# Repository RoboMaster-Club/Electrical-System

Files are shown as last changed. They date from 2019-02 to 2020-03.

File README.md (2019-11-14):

# Robomaster Electrical System Repo
Welcome to Purdue Robomaster Club's Electrical System Repository Created by Chengming Zhang. This repository contain everything from PCB design, Design Notebook (In sub-folder's ReadMe.md), and softwares. 

If you are not familier with Robomaster, or Purdue's Robomaster Team, please refer to [Our Website](https://www.PurdueRM.com "Purdue Robomaster") or check out this video covered by **The Verge**.

<br><br>

<iframe width="560" height="315" src="https://www.youtube.com/embed/ECr4zgK6cPA" frameborder="0" allow="accelerometer; autoplay; encrypted-media; gyroscope; picture-in-picture" allowfullscreen></iframe>

## Team Structure

**Electrical Team Lead**: Chengming Zhang ` @cmz97` 

**Active Member:**

Henry Silva ` @Lazloian` 

Dansen Wang ` @cmz97` 

MingCheng Li ` @blaticslm` 

Ben Mirvish ` @bmivish` 

## Project Structure

📣**For detail design notebook, pls visit the coresponding directory**📣

▶️ Work in-Progress

🔜 Future Project

🉑 Completed Project

🔂 New Iteration

‼️ Need Documentation

⚠️ Ship Blocker

🚮 Abanded Project

<br><br>

The image bellow is our latest **Electrical System Diagram** which lays out all the connection between our subsystems.

 

## Power Electronics

### Super Capacitor Bank ‼️ ▶️ ⚠️

 `Made by @bmirvish @blaticslm`

Due to the competition rule, the robot chassis, which consists of four DJI 3508 geared brushless motor, can not draw more than 240W of power at any given time. To overcome this limitation, we designed our custom made supercapacitor bank as a buffer that provides instantaneous power to our robot on demand. **This Capacitor Bank only consist of voltage banlancing circuit, ADC, and the Super Capacitor Unit.** Since this is a passive electrical unit, there is no firmware.

> Plan for your PCB, Electrical Parameter and Mechinical Parameters like dimentions in your own folder‼️

> * PCB Design  @#todo‼️
> * CAD Design Enclosure @#google drive link‼️

<br>

### Super Capacitor Charger (STM32) ‼️ 🔜 ⚠️ 🔂

`Made by @cmz97`

Since Capacitor is a short circuit when not charged, we need to design a consitance current charger to avoid damage of the battery and capacitor. Chengming Selected to use a H bridge Configuration to create a custon buck convertor using STM32F334. Currently, the Super Capacitor Charger can takes any voltage between 5v - 50v and convert it to 1v - 40v. The maxium output current is 10A. The PCB has a dimension of 2.599 in x 2.487 in and four layer. 

<br>

PCB Design @[SuperCapacitor-v2.0](https://github.com/RoboMaster-Club/Electrical-System/tree/master/SuperCapacitor-v2.0)

Firmware @[SuperCapacitor-v2.0](https://github.com/RoboMaster-Club/Electrical-System/tree/master/SuperCapacitor-v2.0)

<br>

### Power Distribution Boards 🉑

Power Distribution Board is used to distribute electrical current in different voltage across the robot. Currently the Robot takes the following voltage level. 

> **24 Volt** for Robot controller, Any motor

> **12 Volt** for Jetson TX 2, Transparent OLED

> **5 Volt** for Gimbal Electrical Controller Board (ATMEGA), Electrical System Controller(ESP32)

> **3.3 Volt** for all the embedded chip, STM32F4, ESP32, ATMEGA

> **1.5 Volt** for Ammo remaining detection circuit

For a more accurate and compelete report on voltage and current usage of our robot, pls refer to [Power Distribution Board Design Log](https://github.com/RoboMaster-Club/Electrical-System/blob/master/Power-Distribution-Board-V3.0/README.md)

The newst power distribution board is divided into three seperated board:

<br>

### Chassis Power Distribution Board

`Made by @cmz97`

This board provides all the power delivery on the robot chassis, which consist of four DJI M3508 Motor. It also has a 3.3v relay on board that selection output from either the super capacitor bank or the battery directorly. This switching action can be controlled by software via a logic high, which is passed through a opto-isolator  for signal isolation. In case of emergency, such as super capacitor failure, one can flip a by-pass switch that disable all software input, and force the circuit to take battery input only. 

<br><br>

The software switch is controlled by the Electrical System Controller (STM32/ESP32) that switch the output dynamically according to the current power usage. In seniorio such as low votage on super capacitor, Electrical System Controller can select battery input to avoid damage to the supercapacitor, and left it for charging. 

[Chassis Power Distribution Board  Repository for Detail Info](https://github.com/RoboMaster-Club/Electrical-System/tree/master/Power-Distribution-Board-V3.0/Chassis%20Power%20Distribution%20Board)‼️

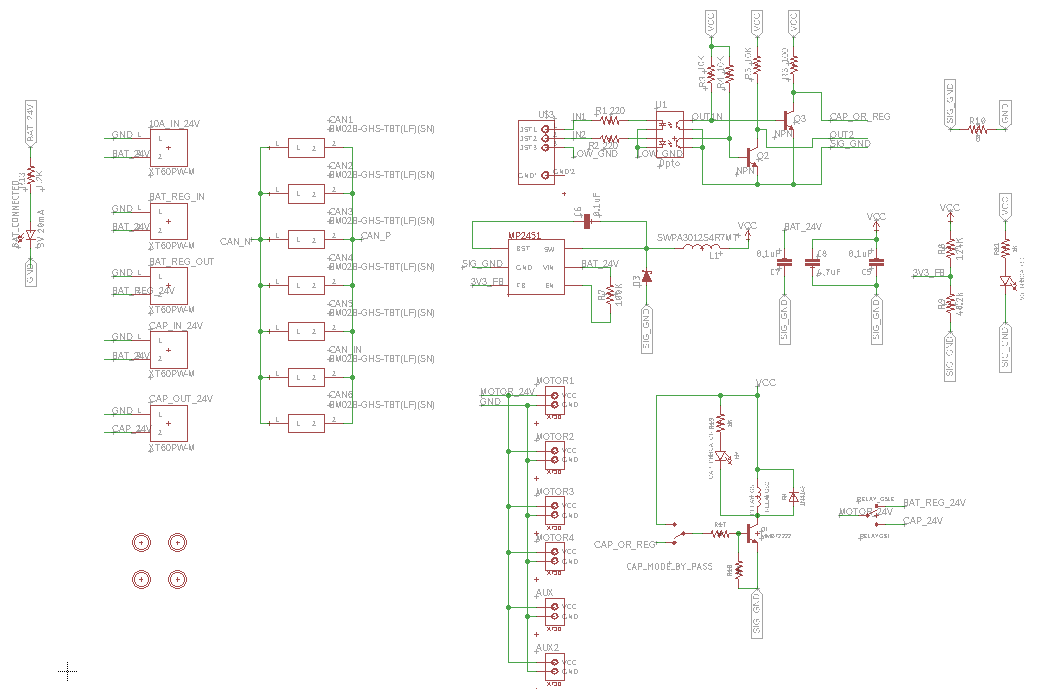
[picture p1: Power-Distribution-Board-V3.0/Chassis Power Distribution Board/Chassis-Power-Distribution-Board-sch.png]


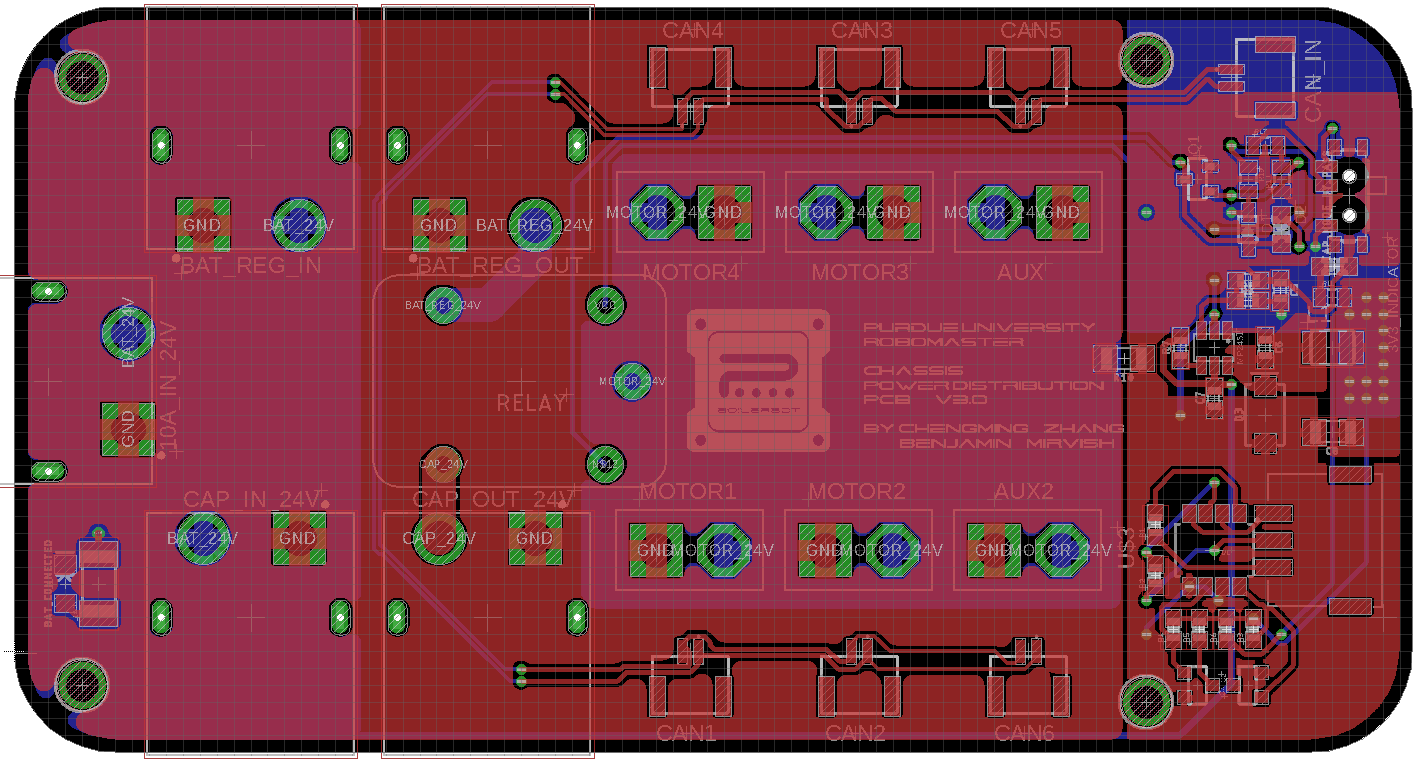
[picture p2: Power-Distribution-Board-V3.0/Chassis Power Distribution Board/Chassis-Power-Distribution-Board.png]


<br>

### Slip-Ring Power Distribution Board

`Made by @cmz97`

This board provides power to the Pitch Motor for the gimbal system, as well as power for Electrical System Controller. The board also provides pre-organization of the wires that go up through the slip-ring. Slipring is used in the robot due to mechanical constraints, where the robot's gimbal needs to rotate continuously. Since there are only 24 wires passess through the slipring used in our standard robot, with each of the wire capable of carring 2A of maxium continouse current, proper signal allocation need to be conducted. <br><br>

We concluded the following wiring asssignment:

| Signal Name | 8A Power | 8A GND | 4A Power | 4A GND | Motor CAN H | Motor CAN L | REF_TX | REF_RX | GPIO | ESP32_TX | Referee System | Ammo Boost |
| --- | --- | --- | --- | --- | --- | --- | --- | --- | ---- | --- | --- | --- |
| # of Wire | 4 | 4 | 2 | 2 | 1 | 1 | 1 | 1 | 1 | 1 | 4 | 2 |
| Max Current (A) | 8 | 8 | 4 | 4 | 2 | 2 | 2 | 2 | 2 | 2 | 2 | 2 |

<br><br>

[SlipRing Distribution Board Repository for Detail Info](https://github.com/RoboMaster-Club/Electrical-System/tree/master/Power-Distribution-Board-V3.0/SlipRing%20Distribution%20Board)

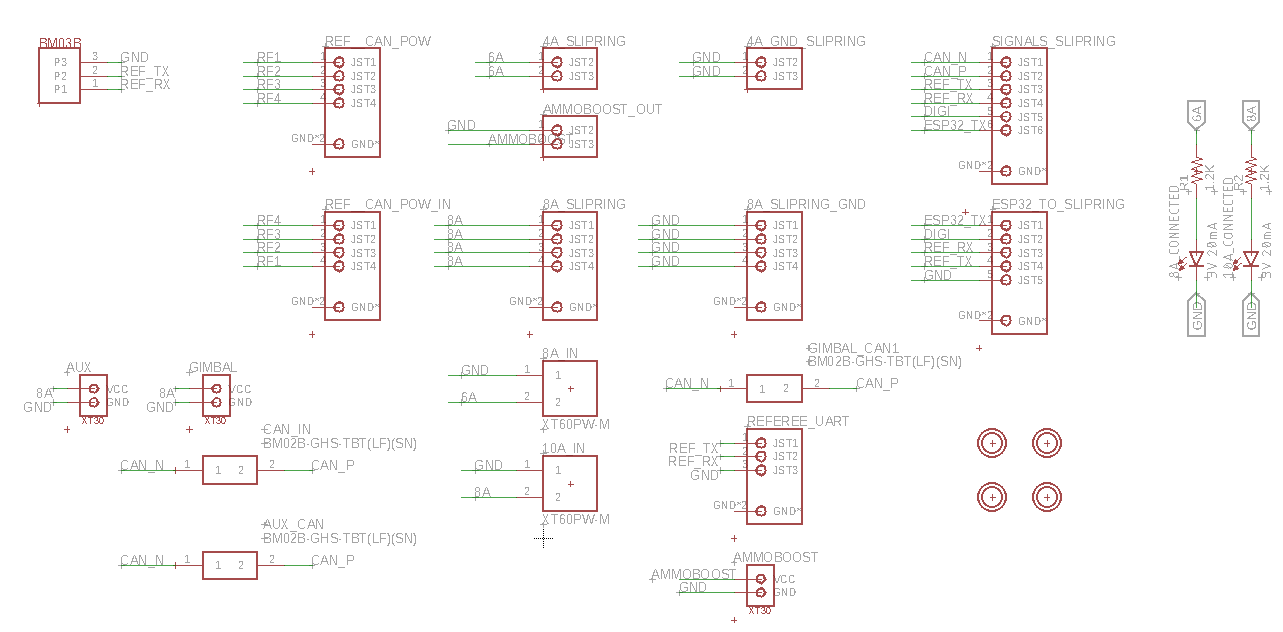
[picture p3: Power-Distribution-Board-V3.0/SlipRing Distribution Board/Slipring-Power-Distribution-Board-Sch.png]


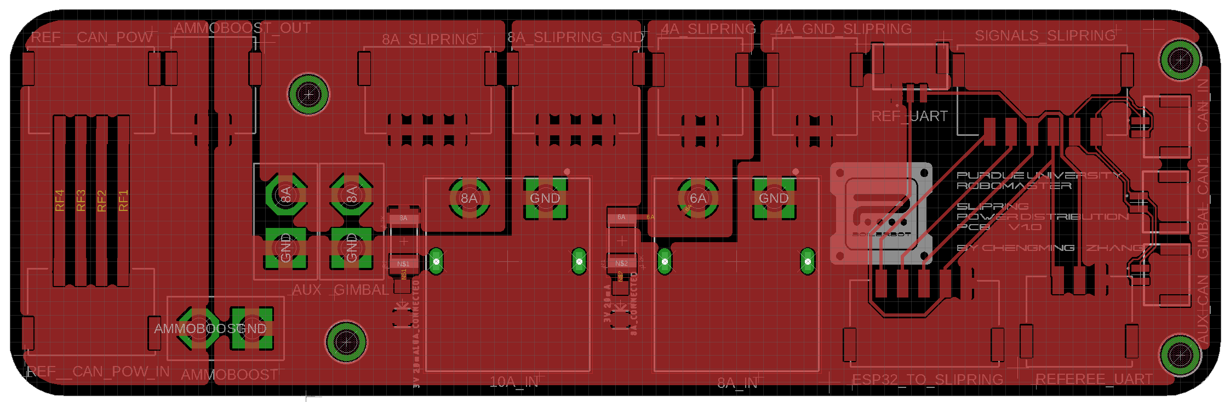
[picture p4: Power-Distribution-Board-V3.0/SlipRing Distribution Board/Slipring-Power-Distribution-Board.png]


<br>

### Gimbal Power Distribution Board

`Made by @cmz97`

This board provides power to the STM32 Robot controller, JetsonTX2, Yall Motor, Flywheel, ammo motor, as well as the Gimbal Electrical System Controller. On board this board, there are two MP1584EN buck convertor that converts 24v from the battery to 12v for Tx2 and 5v for the Gimbal Electrical System Controller.

[Robomater Gimbal Power Distribution Board Repository for Detail Info](https://github.com/RoboMaster-Club/Electrical-System/tree/master/Power-Distribution-Board-V3.0/Robomater%20Gimbal%20Power%20Distribution%20Board)

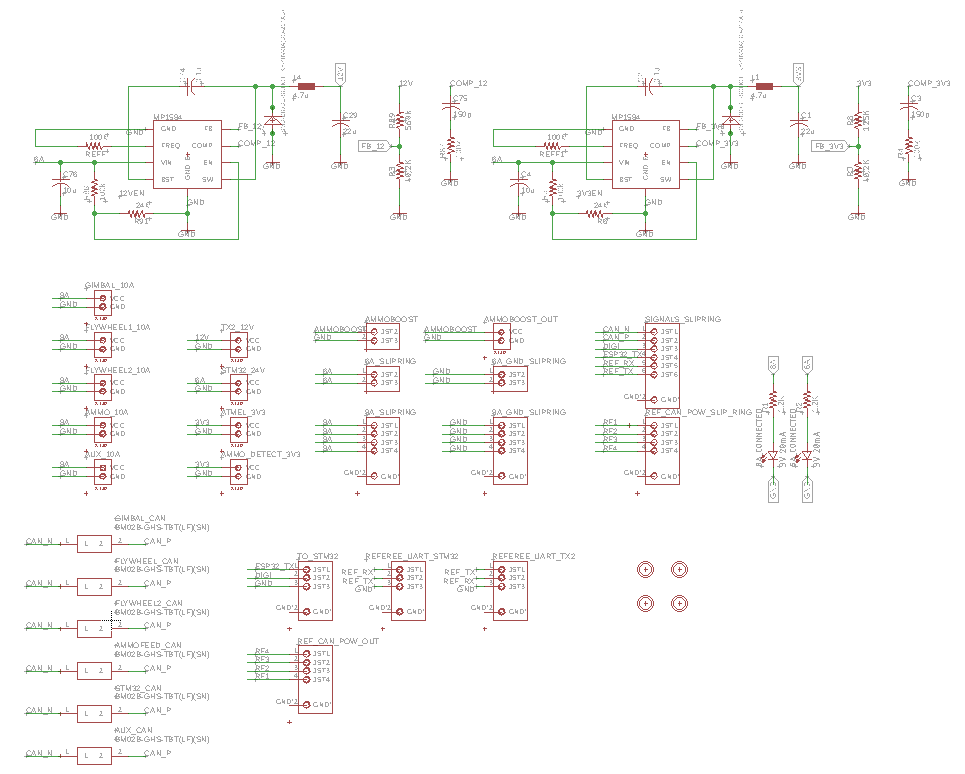
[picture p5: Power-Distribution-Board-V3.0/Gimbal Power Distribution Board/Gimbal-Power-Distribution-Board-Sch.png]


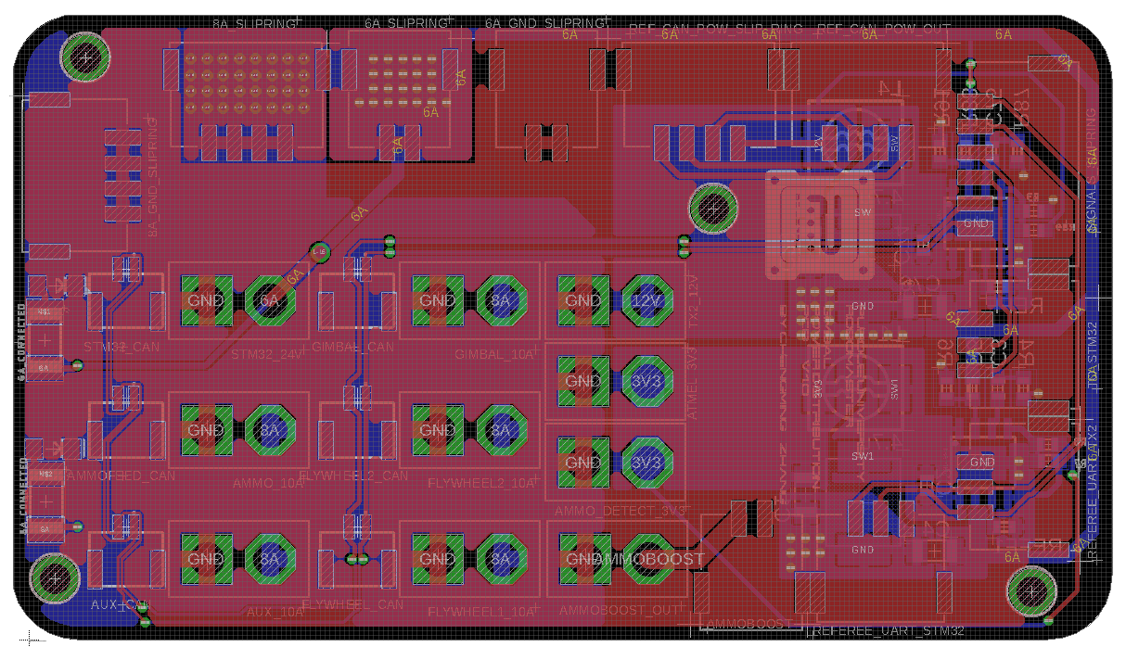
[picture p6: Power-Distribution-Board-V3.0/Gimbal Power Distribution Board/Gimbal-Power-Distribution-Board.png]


<br>
<br>

## Embedded Systems

### Electrical System Controller (STM32) ‼️🔂

* PCB Design `Made by @cmz97`

* Firmware `Made by @William-An`

<br>

### Remote Electrical System Monitor ‼️🔜

`Made by @cmz97`

<br>

### Gimbal Electrical System Controller (ATMEGA) 🔂 ▶️‼️

 `Made by @Lazloian`

  System Controller uses a transparent OLED in front of the driver's camera to display information to the driver. Board recieves info from ammo detector and tof sensors

  HUD Info

  * Lines on the sides indicate walls that are close to the robot

  * Cross hairs in the center of the screen indicate low ammo in the hopper

<br>

### Low Ammo Detection ‼️🔜

 `Made by @Lazloian`

<br>

### Robot Controller (STM32) ‼️

<br>

### Computer Vision System (Jetson TX 2)‼️

<br>

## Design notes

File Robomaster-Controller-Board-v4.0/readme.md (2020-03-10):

# Robomaster-Controller-Board-v4.0:+1:
This board controls the movement of engineering robot's arm and makes it able to grab box of ammos. This board **REQUIRES** 24V Input.

## Components

**Relays**

 There are four relays on the board, three of them controls the robot arm's three different motion: vertical, horizontal, and rotational. The rest one is a back up relay.

**Sensors**
  1. Ammo-Detection Sensor 
  2. Limit Switch
  3. Vision
  4. TOF

**Bluetooth**

Bluetooth enables us to control the engineer robot with our phone.

**Buck Converter**

The buck converter receives 24V input and outputs 3.3V for the microcontroller.

**LED**

LED is for debugging.

## Connectors
| Connector Name  | Connected Object | 
| --- | --- |
| I2C_1 () | IMU (Address: Ch 3, IMU: 1101011 - supply) |
| I2C_2 () | Multi Plexer (Three TOFs) (Address: Ch 1, ToF 1: 1101010 - ground; Ch 2, ToF 2: 1101010 - ground; Ch 3, ToF 3: 1101010 - ground) |
| I2C_3 () | IMU_extra  |
| I2C_4 () | Multi Plexer_extra |
| RELAY1 | Vertical Pneumatic Control (24V output) |
| RELAY2 | Horizontal Pneumatic Control (24V output) |
| RELAY3 | Rotational Pneumatic Control (24V output) |
| CANBUS | Arm Motors |

## Schematic & Board Design
Pin Connections

Micro Controller

Buck Converter

Bluetooth Module

Connectors


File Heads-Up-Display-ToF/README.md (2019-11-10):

# Sensor-Integration

This is the repository for sensor integration on the standard robot and engineer robot

## Overview

The goals of this project are:
1. Use 4 ToF sensors to detect if any walls are close to the robot
2. Display if any walls are close to the HUD
3. Use limit switches on the engineer robot to detect if an object has been grabbed
4. Make a new mount for the HUD
5. Modify or select a new HUD to make it smaller / better

## Contributors

* Henry Silva (PCB Design & Code)
* Dansen Wang (CAD & Mounting)

## Updates

### Update 8 (11/9)

#### Ammo Sensor

Ammo sensor uses laser diode and photo detector to determine if ammo in the hopper is low. PCB is a ring that is placed in the hopper with diode mounted on seperate board.

### Update 7 (11/1)

#### HUD

Added low ammo indicator. Represented by four dots in the center of the screen. Wall indicator updates made faster by reducing the number of sensor readings to take the average of and by alternating pixels on the display.

#### Control Board

Finished soldering prototype, testing and final changes will be made this week.

### Update 6 (10/26)

#### ToF Code

New method for clearing the screen fixed problem of long pause in program. Wall indicators made thinner to make room for other indicators.

Under current refresh rate, hud updates can be made faster depending on the number of times to read the tof sensor. Tests concluded that 3 tof readings before taking the average is fastest while not having false positives.

The left and right tof sensors on the front and back of the robot now have different indicators for walls to give driver a better understanding of where the walls are.

Indicators added at startup to show when the hud is ready.

Demo

Demo

### Update 5 (10/19)

#### HUD Mount

A camera holder and a bracket for the OLED screen was CADDed.
Camera Mount
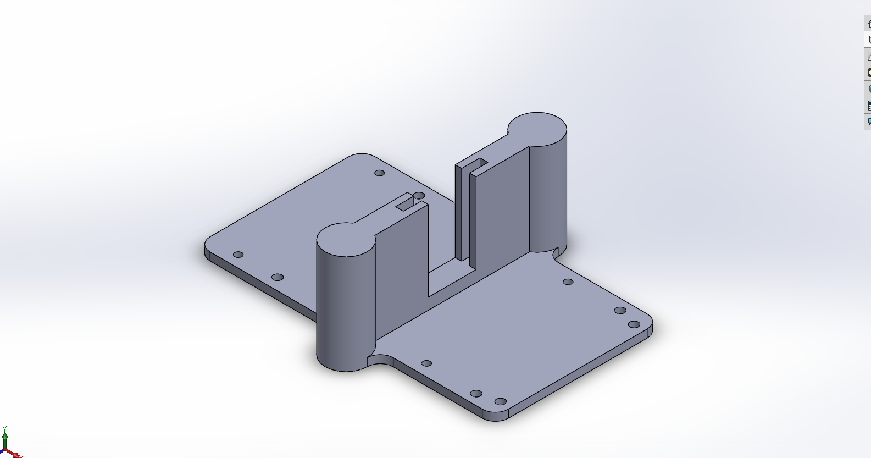
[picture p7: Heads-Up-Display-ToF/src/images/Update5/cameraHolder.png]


Bracket for OLED was first 3D printed out with multiple slots signifying different distance the OLED screen is from the camera.

Test
Test

With further testing, the ideal distance between the camera lens and the OLED screen is 0.35 inches. Modifications were made, and the OLED bracket was modified

Mount
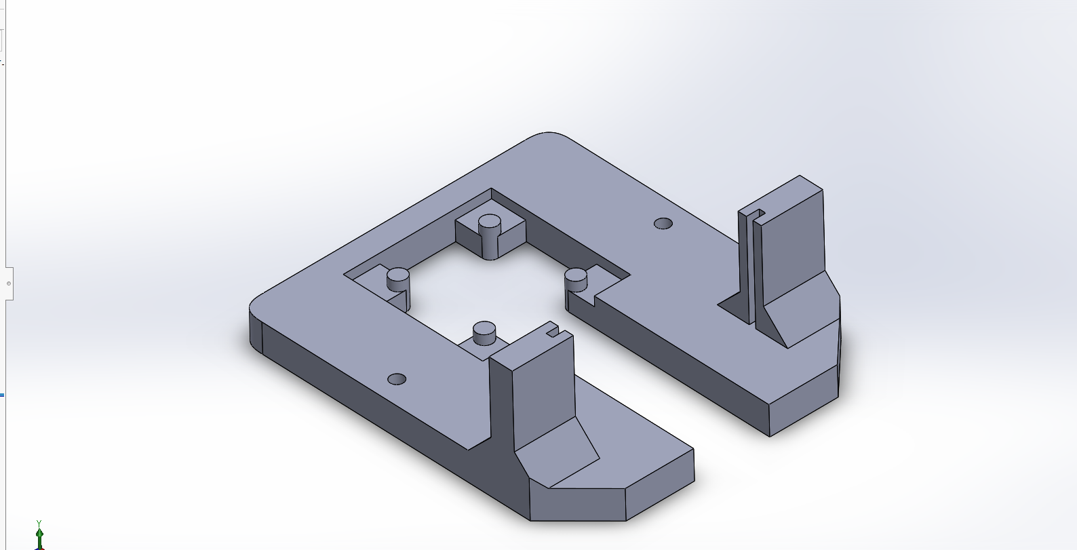
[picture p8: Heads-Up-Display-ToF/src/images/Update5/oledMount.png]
Mount


Demo of the camera and OLED

Demo
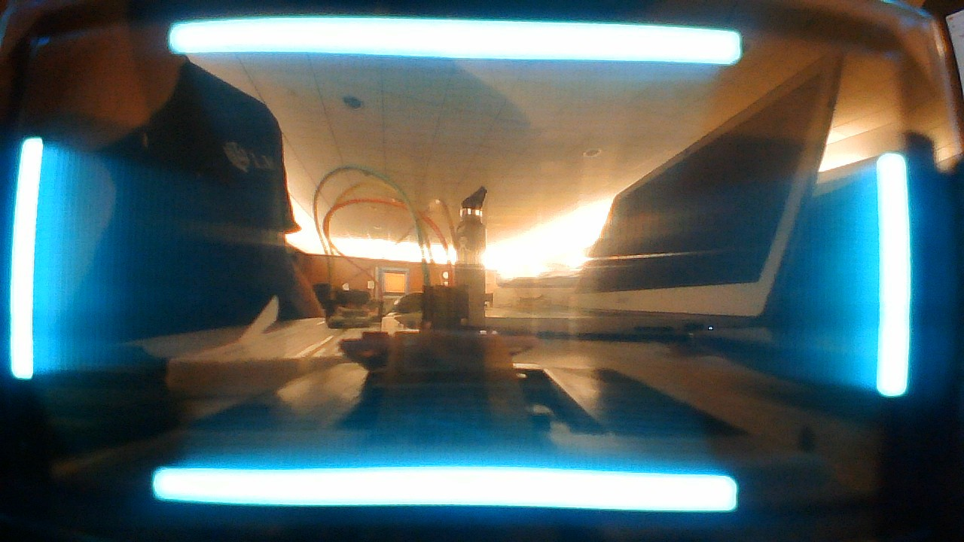
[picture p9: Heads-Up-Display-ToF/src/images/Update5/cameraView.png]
Demo


A case to hold the photogate sensors was CADDed out as well. It's a simple plastic case with very low tolerance around the dimensions of the sensors. The case will then be glued onto the body of the robot.

Sensor Casing
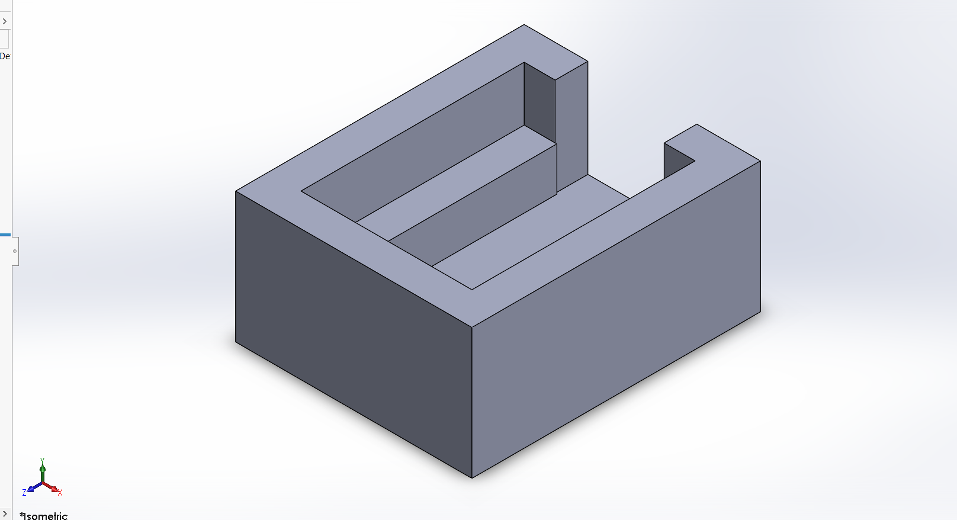
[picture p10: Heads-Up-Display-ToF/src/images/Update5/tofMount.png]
Casing


#### OLED Control Board

Final update to the pcb. Changed button to a smaller one. XT30 for power was added. Boost was improved by adding polygons and vias. Switched from micro-USB to USB-C.

Schematic
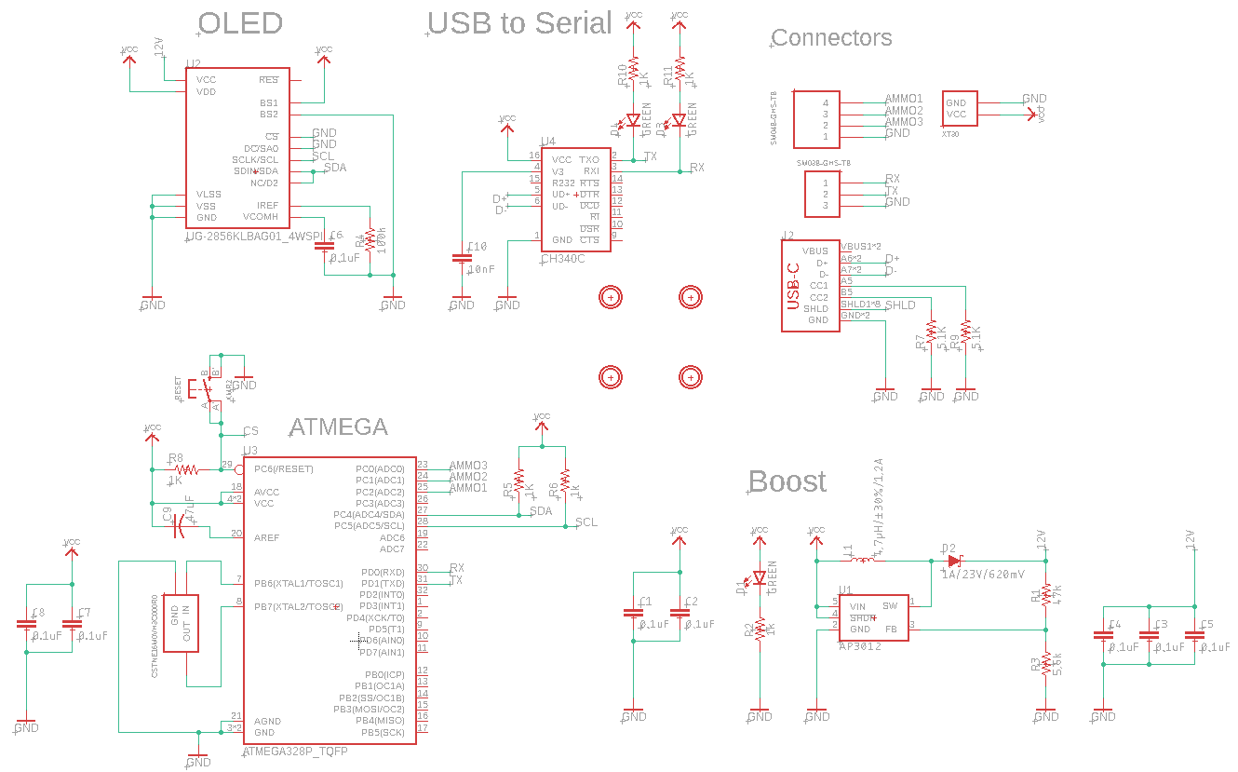
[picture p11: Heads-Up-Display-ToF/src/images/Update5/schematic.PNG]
Schematic


Board

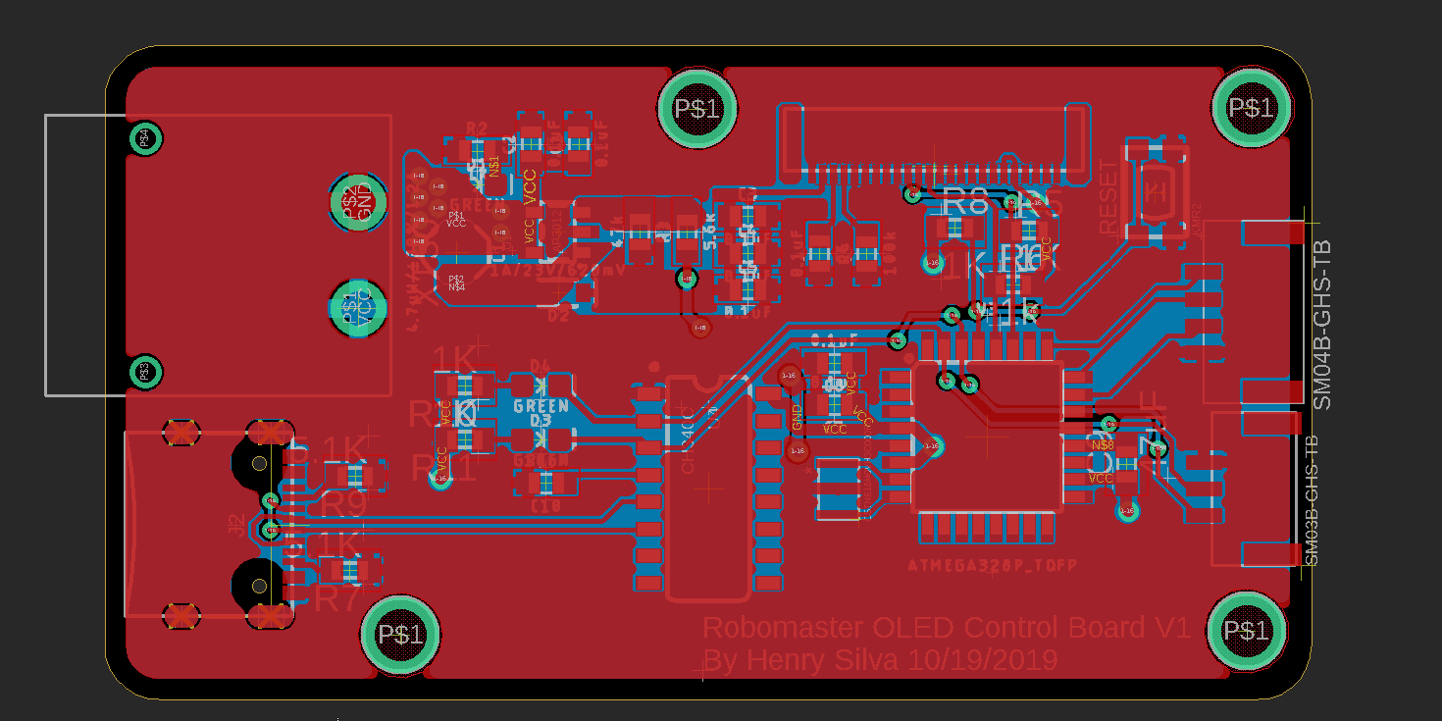
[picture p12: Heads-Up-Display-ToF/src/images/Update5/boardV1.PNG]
Board


### Update 4 (10/12)

#### Wall Detection

Tested final code on breadboard. Code mostly worked, but is running slowly. I think it is because of the OLED screen and the time it takes
to clear the screen. Solution is to only update the screen when necessary (keep track of what the OLED is already displaying and only update when needed)

#### OLED Control Board

Finished schematic for control board. Added USB to serial converter with the ch340 chip, reset button for the atmega, 3 pin JST connector for the ammo sensor, and micro usb connector for programming the atmega.
Decided on placement of components on board.

Schematic
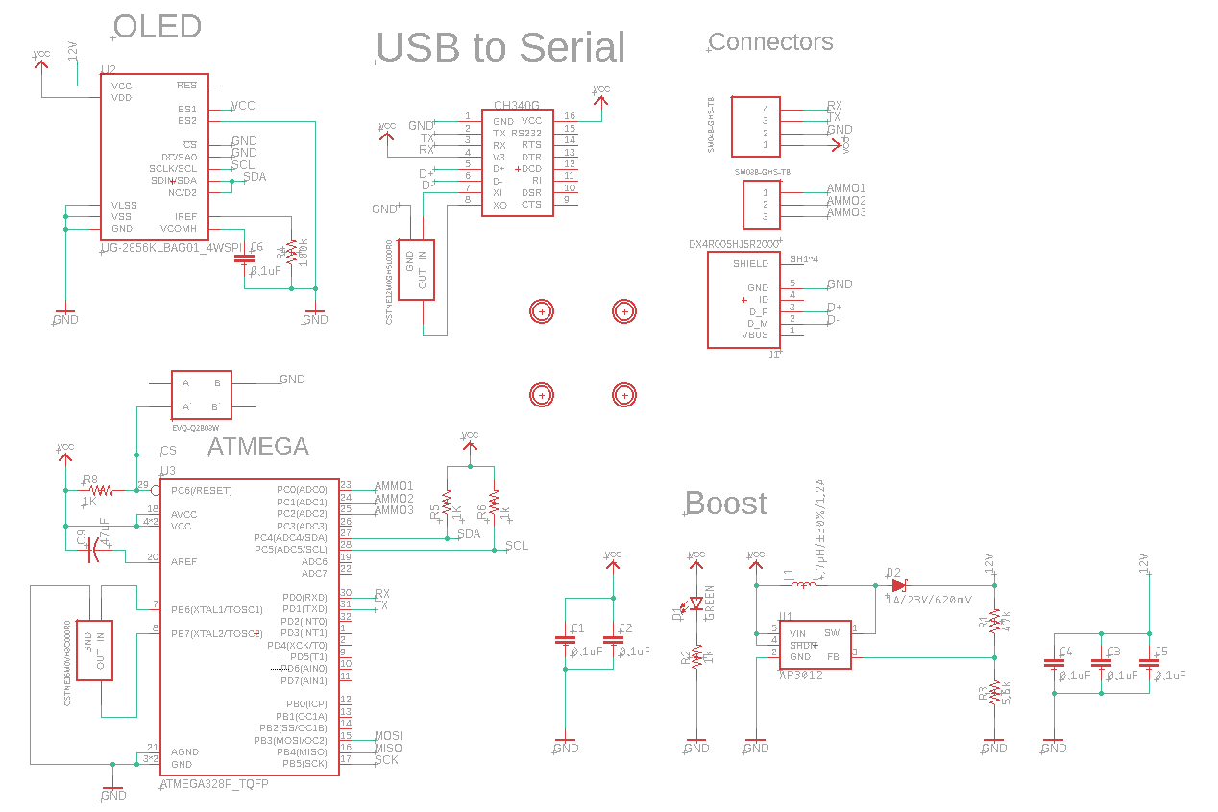
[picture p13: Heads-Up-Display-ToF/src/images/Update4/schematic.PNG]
Schematic


Board
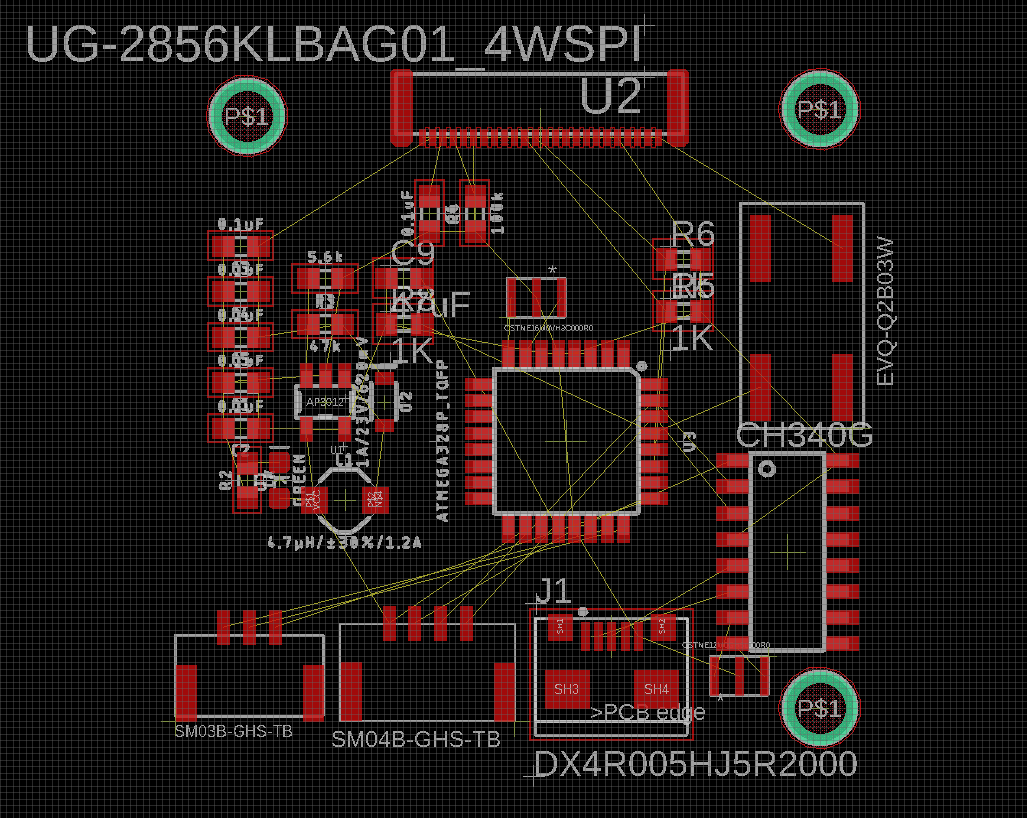
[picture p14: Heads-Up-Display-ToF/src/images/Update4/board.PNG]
Board


### Update 3 (10/7)

#### HUD Mount

A exact replica of the plate gap in front of the camera, with a holder in the middle to hold the camera, simulating camera placement.

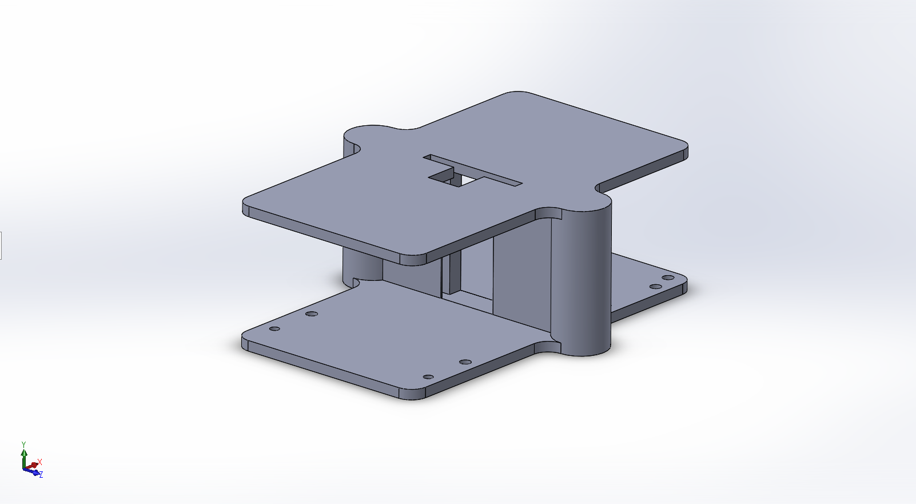
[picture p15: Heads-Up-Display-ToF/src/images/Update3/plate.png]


Mark 1 of the OLED holder, without mirror focal length calculation and OLED size on overall camera FOV consideration

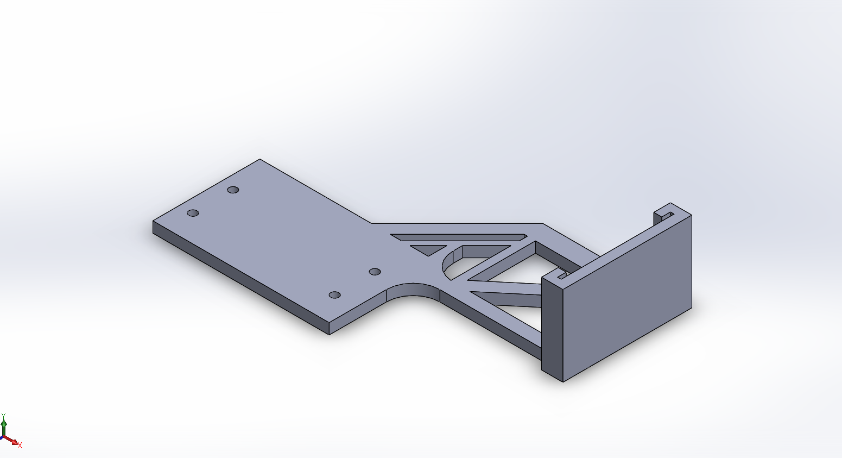
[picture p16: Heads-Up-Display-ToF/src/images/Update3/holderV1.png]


Mirror Drawing

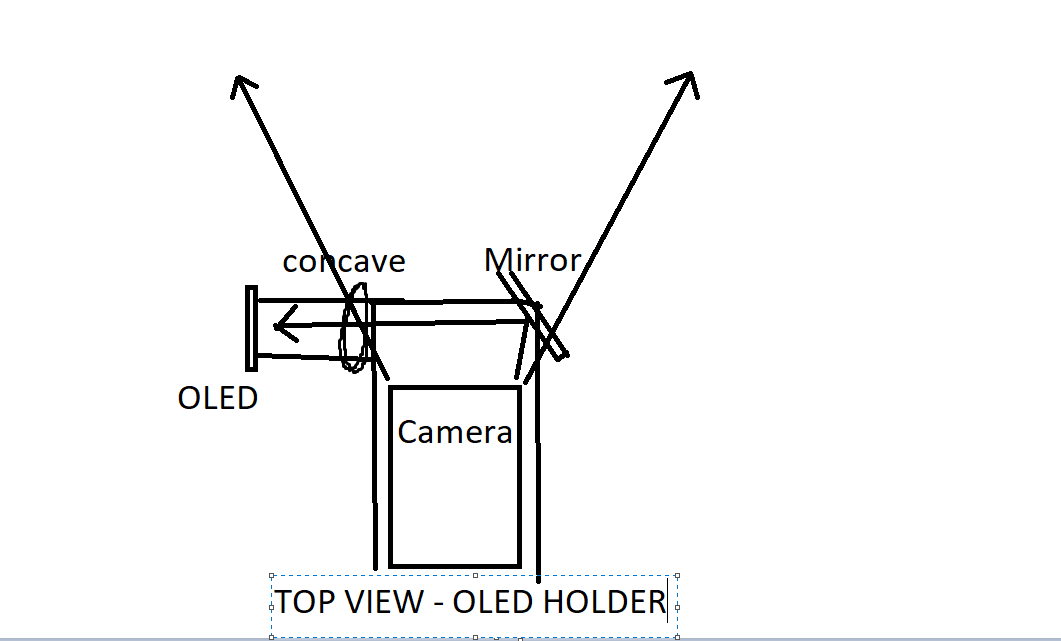
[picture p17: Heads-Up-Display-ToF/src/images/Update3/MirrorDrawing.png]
Mirror Drawing


#### Wall Detection

Finished first version of code to show close walls on the HUD. Uses timed interrput to get sensor measurements every 4 milliseconds and update the OLED every 20 milliseconds. Average of sensor values in between OLED refreshes is used to determine close walls.
Currently untested, but will test before the next update. Planning to have the direction of the close wall be relative to the current
angle of the gimbal.

#### OLED Control Board

I chose the ATMEGA328p-au as the microcontrller. The board will have one connector for the OLED and 2 4-pin JST connectors for communication 
between the DJI control board and programming the microcontroller. No mounting holes have been added.

Schematic
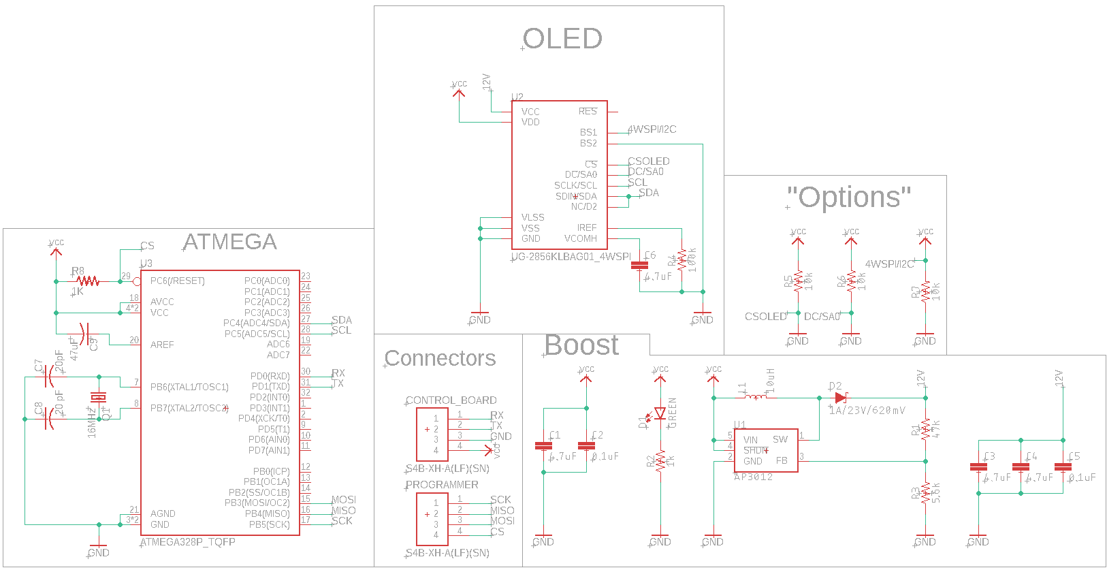
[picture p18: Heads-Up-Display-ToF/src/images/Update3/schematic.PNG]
Schematic


Board
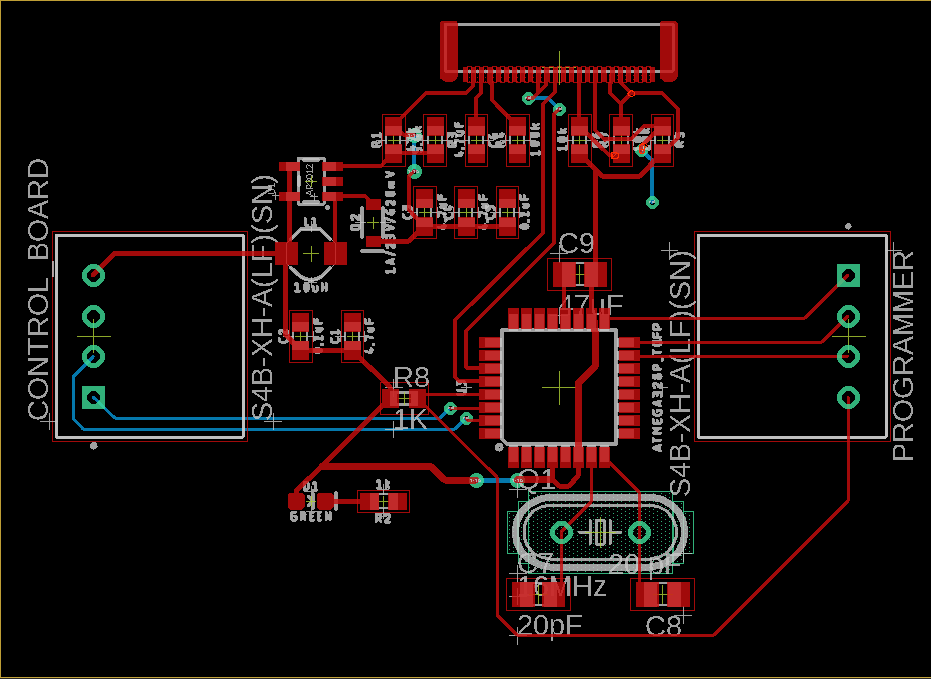
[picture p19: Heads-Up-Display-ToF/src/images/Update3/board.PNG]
Board


### Update 2 (9/28)

Made first schematic for smaller OLED breakout board. Removed all SPI related components and pins. Removed options.

SchematicV1
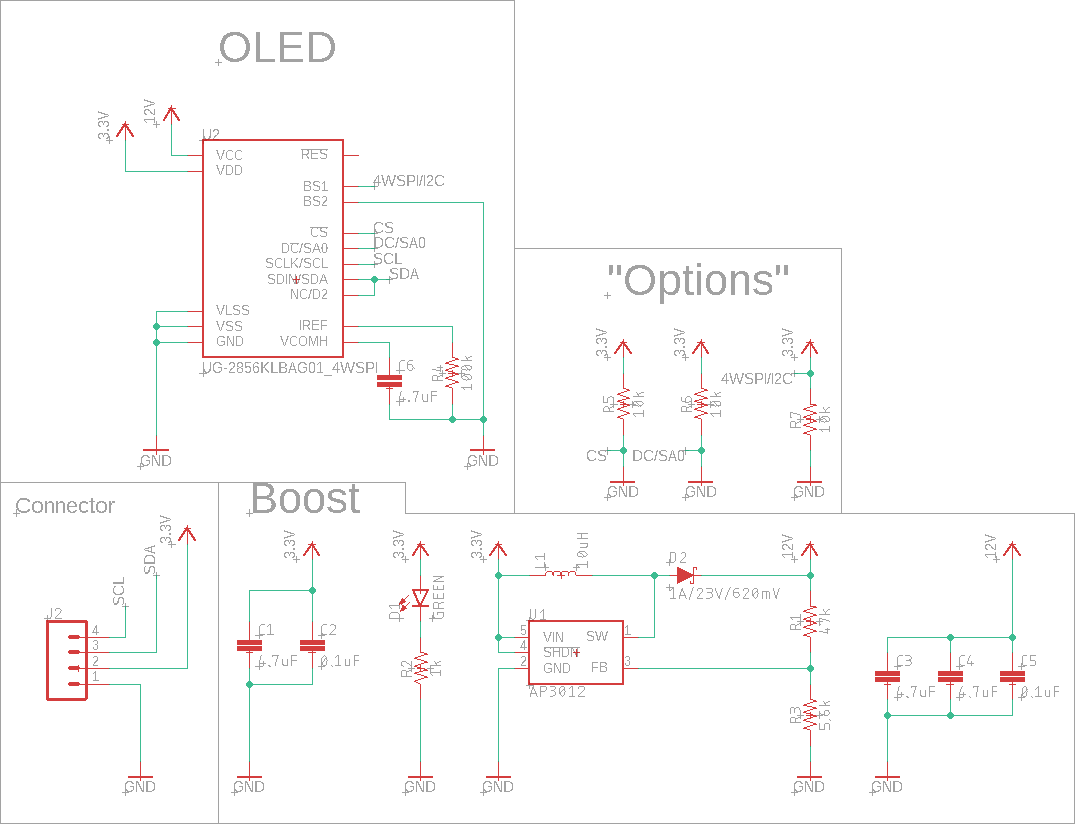
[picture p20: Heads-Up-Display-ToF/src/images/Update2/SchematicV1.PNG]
SchematicV1


Two concept drawings for the HUD element giving the driver the information about close walls. Concept 1 takes up less space and is easier for the driver to see at glance. Concept 2 is more specific, but it is up to the drivers.

Concept 1
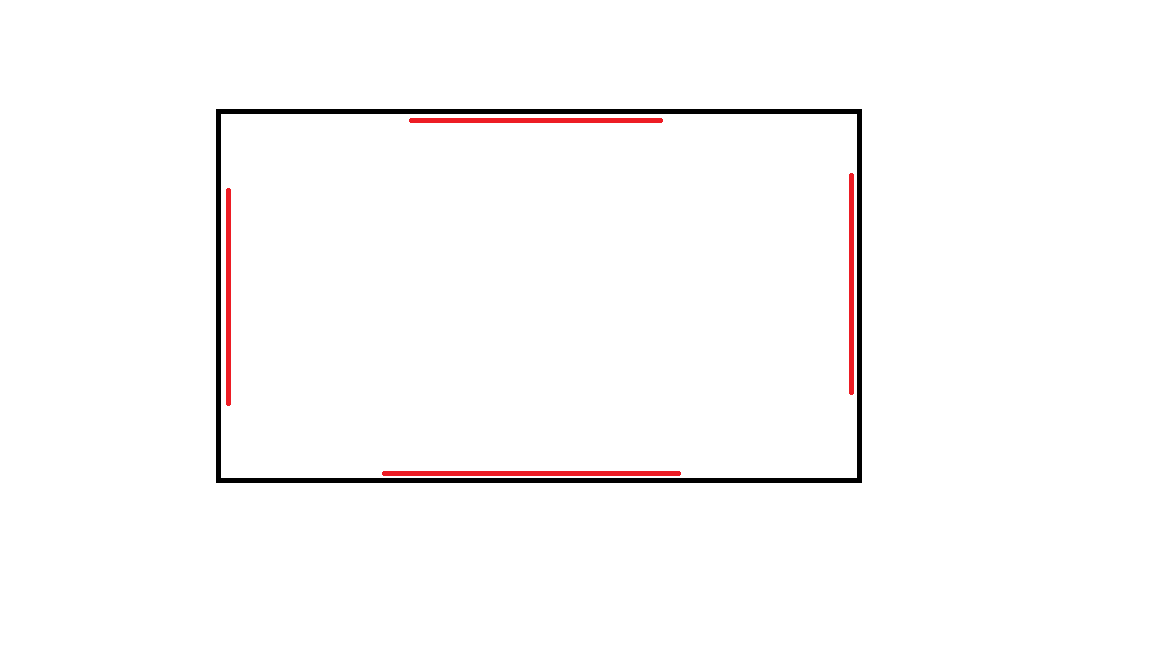
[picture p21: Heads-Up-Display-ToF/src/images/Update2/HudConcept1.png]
Concept 1


Concept 2
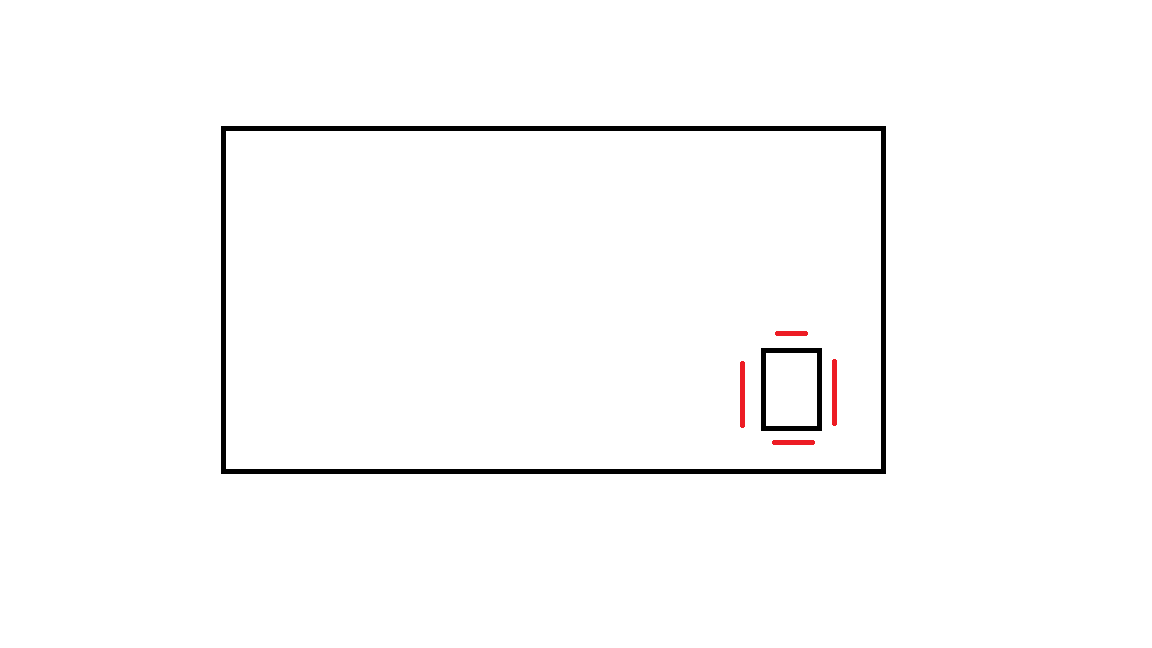
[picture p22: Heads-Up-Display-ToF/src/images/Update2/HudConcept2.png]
Concept 2


### Update 1 (9/21)

#### HUD Mount

Mating Example
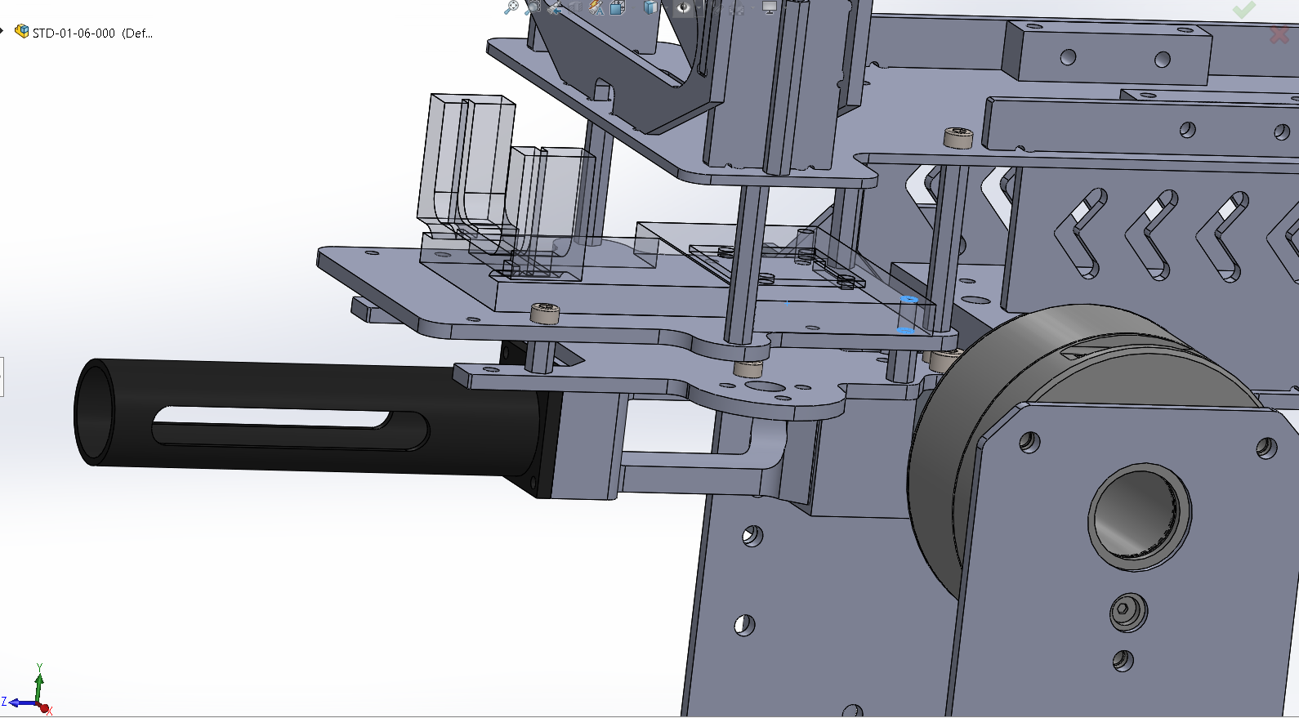
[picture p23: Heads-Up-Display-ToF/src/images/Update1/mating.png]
Mating Example


Part
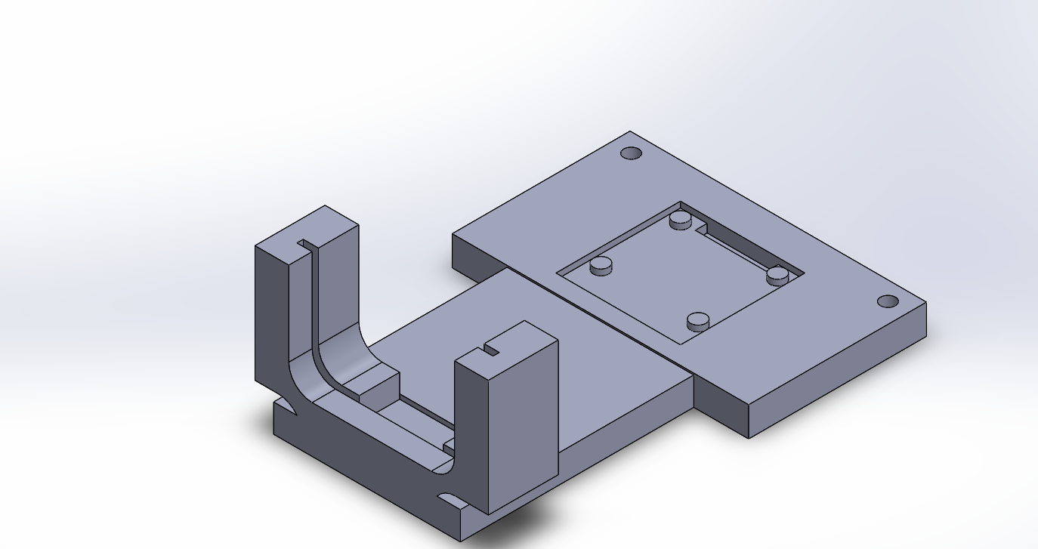
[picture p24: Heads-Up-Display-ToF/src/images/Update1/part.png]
Part


Concept
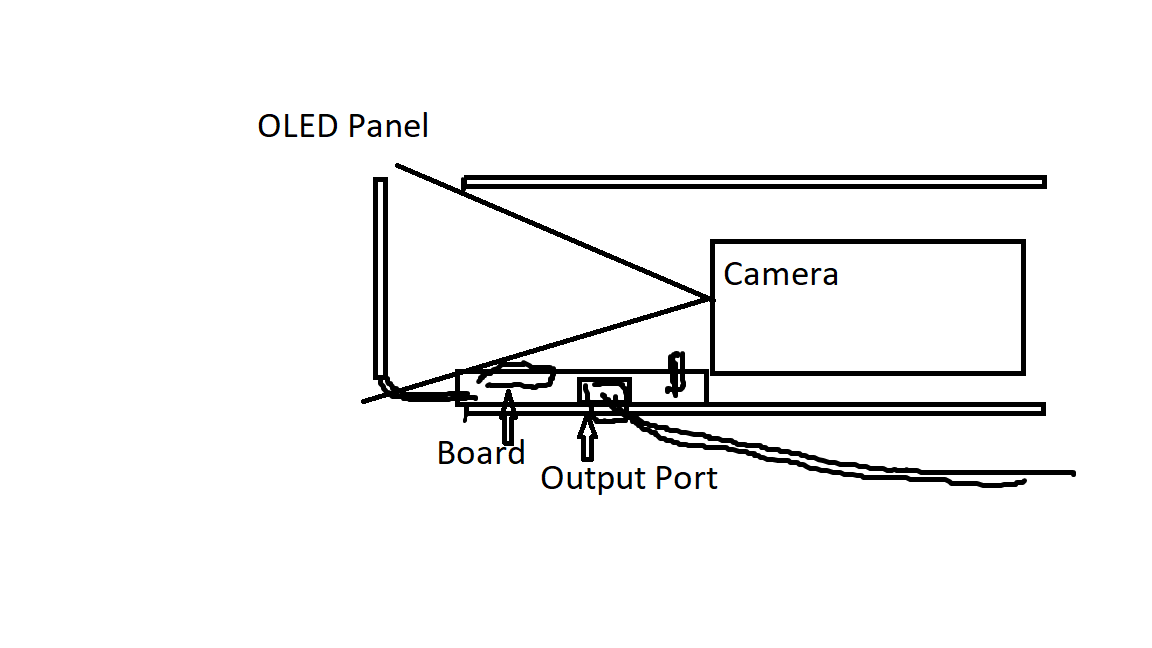
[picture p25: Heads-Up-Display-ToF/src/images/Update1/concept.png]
Concept


#### ToF Integration

Got sensors to output values of 2 ToF sensors(should work for 4). Determined a measurement of 300mm to be a wall that is "close". 

Serial Output

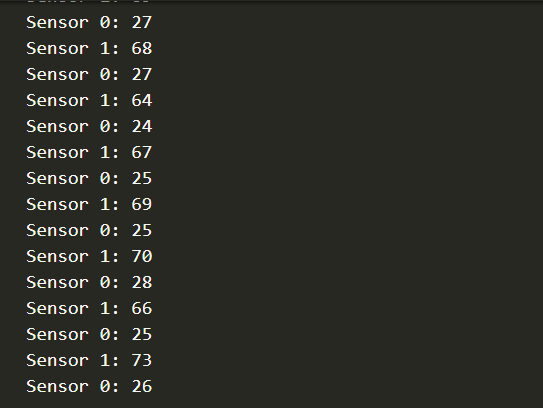
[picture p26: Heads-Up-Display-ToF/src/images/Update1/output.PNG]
Serial Output


Model of Wall Detection
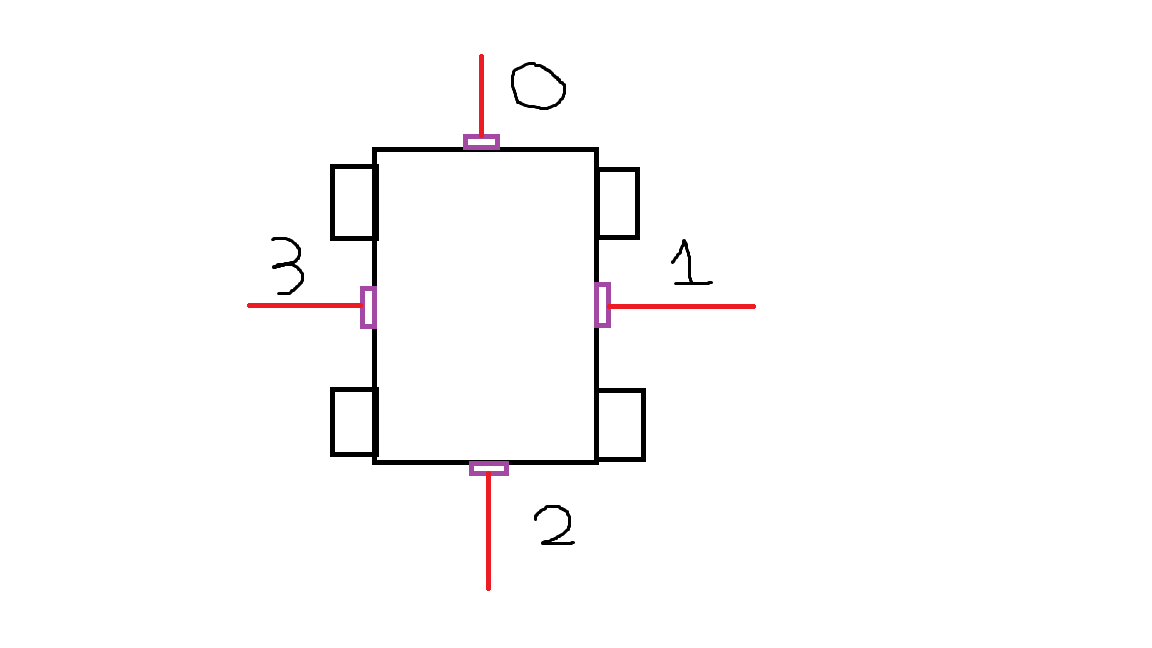
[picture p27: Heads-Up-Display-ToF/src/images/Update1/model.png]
Model of Wall Detection


Sample Output

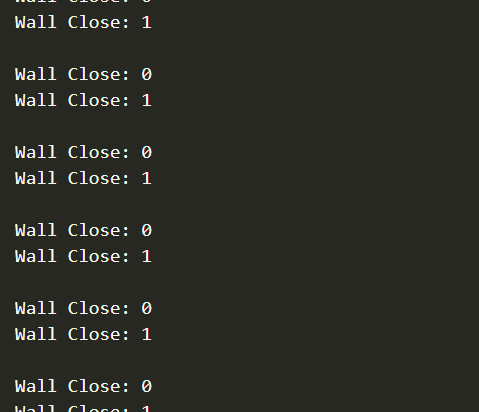
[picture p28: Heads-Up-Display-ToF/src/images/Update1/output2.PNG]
Sample Output


Researched interrupt for VL53L0X sensor. Tried what might of been the interrupt pin on the current breakout board and it did not work.

Pinout
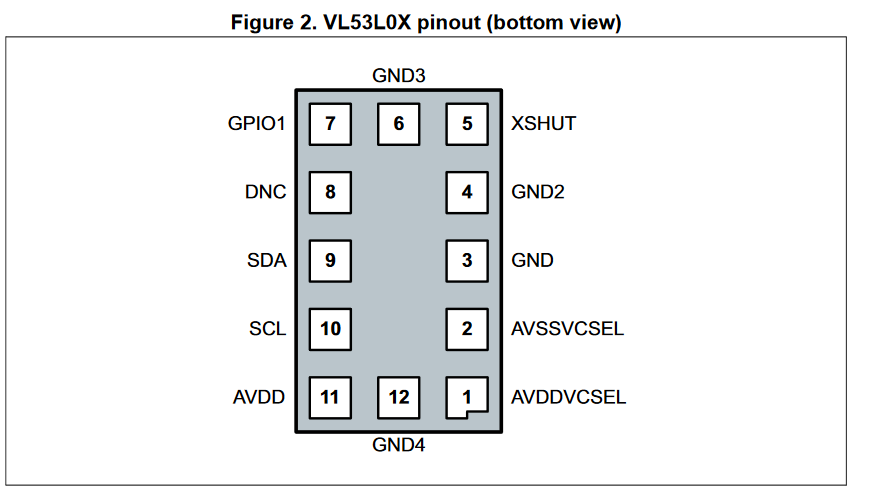
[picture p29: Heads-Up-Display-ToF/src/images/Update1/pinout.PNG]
Pinout

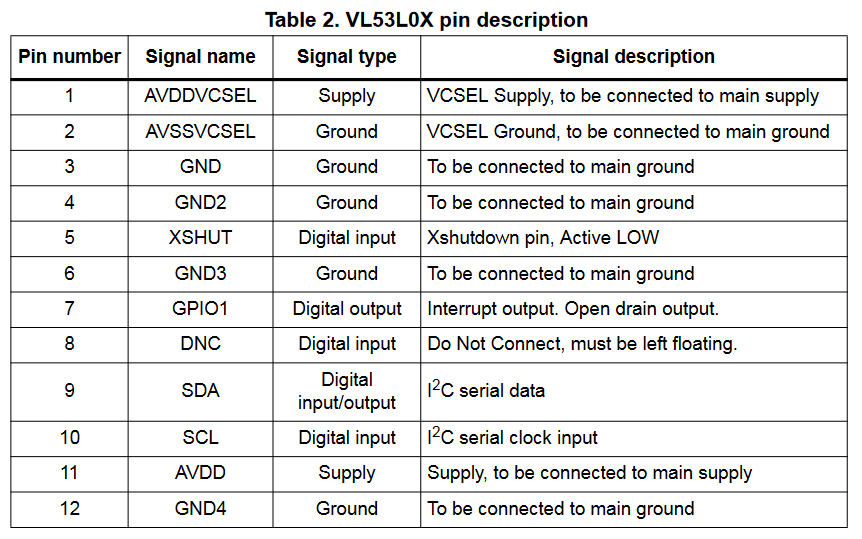
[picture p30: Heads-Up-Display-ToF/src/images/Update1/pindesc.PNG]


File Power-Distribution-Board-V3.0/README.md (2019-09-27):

# **NEW power distribution board**
> Based on the new rules, there will be a power distribution modulus and outputing 2x10A, 1x6A, and 1x8A(reserved)

## **Stage - Data acquisition and pre-design**
> This is for optaining the useful data to do the primary design

### 09/14/2019
- the data was measured from current meter
- 4 x Wheel motor
- 1 x Firing motor (Fly wheel motor)
- 1 x Gimball pitch motor (up-and-down)
- 1 x Gimball yaw motor (Left-and-right)

QQ截图20190915025746

>Problems found
- Nvidia TX2 needs at least 8A current
- 4 x Wheel motor: Must < 4.5A
- 2 x fly wheel motor: overpowered, but now fixed

>To do next
- Get the first PCB design out: for 10A? (FOR NEXT WEEK)
- Measure the firing motor current
- Draw the diagram of the Power distribution board

### 09/27/2019
> The specific current capacities for two 10A rail and 6A rail are below
- 10A rail 1
> 10A-A

- 10A rail 2
> 10A-B

- 6A rail
> 6A

- To do next
> Keep doing the PCB for 10A rail A and B schemetic (By Saturday)

> Measure TX2 current

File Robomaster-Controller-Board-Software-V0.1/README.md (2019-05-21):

# BoilerBot Electrical System Monitor v0.0.1a

This folder contians the source code for BoilerBot electrical system monitor, which is consisted of two components: sensor data collection and web interface.

The sensors the system will receive data from include:
  1. 6x [VL53L0X Time of Flight Distance sensor](https://www.adafruit.com/product/3317)
    1. 1x Measure the vertical distance between the climber and the ground
    2. 2x Measure the forward distance between the robot and the island
    3. 1x Rear Forward distance measurement
       1. Check when should robot lift rear leg 
    4. 2x Grapping arm distance sensing
       1. Check whether grabed armor box
 1. MCP9808 Temperature sensor
 2. PCF8523 RTC module
 3. Battery voltage analog input
 4. Battery current analog input
 5. Supercapacitor voltage analog input

After finish reading data from sensors, the mcu will packet all of the result into a custom struct with the following format, serialize it using `union`, and broadcast it on the websocket channel to be displayed on web interface.

    struct Measurement
    {
      uint32_t timestamp;
      float vbatt;
      float vcap;
      float ibatt;
      float tempC;
      bool ableBoost;
      float vertiDist;
      float leftDist;
      float rightDist;
      float rearDist;
      float leftGrabDist;
      float rightGrabDist;
      bool isLeftClaw;
      bool isRightClaw;
    };

Meanwhiile, this data buffer will also be stored to microsd card in a file named with the time and date the board power on and its content can be decoded using the decoder python script under the `utils/` foler.

The web interface part mainly provides graphical representation of the sensor values and access to on board log files. In addition, it also provides simple setting to the system like configuring SSID and password or sensor sensitivity. It can be accessed by connecting to the WiFi of the on board ESP32 (`BoilerBot_TYPE_NUM`) and then one can visit `boilerbot.local/` or `192.168.4.1` for the interface.

Web interface

## Usage

1. Install Arduino IDE 
2. For VSCode development
      1. Open `.code-workspace` configuration file
      2. Or install Arduino extension by Microsoft
3. Install ESP32 board in Arduino IDE [here](https://github.com/espressif/arduino-esp32/blob/master/docs/arduino-ide/boards_manager.md)
      1. For vscode
         1. Use Board manager of the arduino extension
         2. Press `ctrl/cmd + Shift + P` and type `arduino board manager`
         3. Search `ESP32` and install it
4. Install CP2102 Driver (or other kinds, depend on your chip) for USB2UART
5. Install necessary third-party library
     1. [ESPAsyncWebServer](https://github.com/me-no-dev/ESPAsyncWebServer#installation)
     2. [AsyncTCP](https://github.com/me-no-dev/AsyncTCP)
     3. Adafruit_MCP9808
     4. RTClib
     5. Adafruit_SSD1306
     6. VL53L0X by pololu
6. Configure include path for vscode
      1. Open `.code-workspace` configuration file
      2. Modify the path so that they match your computer's setting
      3. [ ] Todo: use system path?
7. Compile and upload `global.ino` to the ESP32

## Todos

### Functionality Test from Power Dis
- [ ] Control of Relay (Cap or not)
- [x] Temperature Read
- [ ] Current Read (I2C)
- [ ] Read of battery voltage (I2C)

### Functionality Test from Controller Board
- [x] Able to Program
- [x] Able to reset
- [x] SD read and write
- [ ] MCP2300x Testing
- [ ] Reading from new power distribution board
- [x] TCA9548A
  - [ ] Note that the onboard TCA chip on the test board might be damaged as it cannot properly select port sometimes and the #1 port on it cannot communicate with sensors
- [x] Timer
- [ ] System Stability Test (Connect all peripheral)
- [ ] Buzzer (DJI)
  - [ ] Achieve intel sound
- [ ] All I2C peripherals
- [ ] Digital limit switch
- [ ] UART Protocols to STM32F4
- [ ] UART Protocols to STM32F3

### Updates Power Dis
- [ ] Check Relay
- [ ] Check Switch by pass

### Update Super Capacitor Charging Board
- [ ] Read of all voltage
- [ ] Read of all current
- [ ] UART all functionality
- [ ] PID

* Sensors
  * [x] Data Logging
  * [ ] Handle sensor disconnection
  * Sensors reading
  * Use led to indicate status and error
* Serial
  * Create debug port?
  * Bluetooth Lib too big [Solution](https://github.com/SensorsIot/Bluetooth-BLE-on-Arduino-IDE/issues/3)
* Threading issue?
* Web
  * Speed increasing?
  * Turn off animation
  * Log
    * Log file management
    * Log file download
    * Log file plotting
      * [ESP32 SD Flush not working](https://github.com/espressif/arduino-esp32/issues/1293), use newest release version
  * Reconnection button
  * Status
  * setting
    * Set mode of system
    * Set ssid, pass, hostname (eeprom)
  * Embed css and js files to avoid running out of mem?
* Extendability
  * Able to use in the next season
* API Explanation
* `/`
  * Handle logging chart display
* `/log`
  * Provide logging file downloads 
* `/status`
  * Whether each module is online or not
* `/setting`
  * Mode selection
    * Super cap MODE
    * mix mode
    * battery only mode
* WebSocket Event
  * connect
    * server broadcast current sensor data to this client
  * disconnect
    * cleanup
  * data
    * sensor data
* Library
  * Better include method
* Performance check

## Contributors

Charlotte Huang, Roshni Sarma, Megan Singer, William An

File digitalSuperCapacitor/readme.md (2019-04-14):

# **Supercapacitor power distribution test**
> For validating the design, it is necessary to simulate or create the actual circuit to see whether the design matches the expection. 

## **code has been in the folder**

## **Stage 1**
> Feb,2,2019

Validating the charging, discharging, and detection functionality by using Analog output

>**Charging Circuit**
- discription: A1 is to control the charging current flow and set the voltage P1 to turn on MOSFET P1
- P1 links to MOSFET gate, and Vgate to source should be -10V


qq 20190208082002

>**Discharging circuit**
- discription: A2 is to control the discharging of the supercapacitor to turn on MOSFET P2
- Vgate to source of MOSFET P2 is -8V with 8bit analog output value 255

qq 20190208072129
mosfetp2

>**Detecting circuit**
- discription: The purpose of this circuit is to detect the supercapacitor's voltage by analog input
- Failed, it needs to be redesign. 
- After analog input reading reaches 76/1023, the value stays constant

qq 20190208070718

## **Stage 2**
>Feb.15, 2019

Supercapacitor voltage detecting circuit modification

>Board modification
qq 20190222134428
- The diameters of the connector holes expand to 0.95mm due to wrong calculations(P4 and P2 connector)
- MOSFETs (Bottom 2 red areas) and  Schottky diode array (upper right) are placed on the exposure copper plate (red area). 
- Some wire widh has been adjusted. 
- circuit detecting circuit has been formally modified (first time). 
- P2 connection has been changed to 5V from A3-detect. 

>Detection circuit
- Read the value correctly from A3-DETECT

qq 20190222140208

>Next Plan
- Go EE to get components. 
- Test Supercapacitors: teammate responses for.
- Learn LT SPICE with Matthew. 
- Overall supercapacitor program in Arduino. 

## Stage 3
* (finishing testing and more ideas on modifying the board design.) 
* Code has been in the folder. 

### Competing with being "nothing". 
> Some problems has been excountered. 
* Ground has been exposed outside the board, causing fatal short that penetrated the FKBJT.
* IN and OUT ports for Voltage stablizer and amplifier are not standardized designs.
* Charging, discharging, and detecing circuits' width is not enough.
* BJTs is very stupid that easy to die in front of me. 
* Detecing circuit is not functioning. 
* Spacing arrangement of the circuit can be improved. 

* * * * * * * * * * * * * * * * * * * * * * * * * * * * * * * * * * * * *

> Improvement that can be done
* IN and OUT ports for Voltage stablizer and amplifier, VCC, Capacitors, and Motor connectors should change to [XT60 series connector](https://www.amazon.com/OOOUSE-XT60-Connector-Pairs-pairs/dp/B005FAPYXS) for better design integration.  
* All the BJTs should switch to MOSFETs for reliability. 
* All the circuit should have lower power LEDs for indicating the circuits' validation and decent labels for each funtionality. 
* Detecting circuit must be modified. 
* The board can be larger for better spacing arrangement and larger trace width. 

* * * * * * * * * * * * * * * * * * * * * * * * * * * * * * * * * * * * *

> Next Stage
* New design
* New Programs values. 

## Stage 4
* New, modified design has been here now. 

### Schematic and Board
QQ截图20190412221912
Modified Circuit design

### Modifications. 
* All connectors except microcontroller input have been changed into [XT60 series connector](https://www.amazon.com/OOOUSE-XT60-Connector-Pairs-pairs/dp/B005FAPYXS). 
* All BJTs have been changed to 40V 5A MOSFET - All the circuit will not need analog output to control anymore. 
* The discharging and charging circuit for supercapacitor have individual LEDs to indicate circuit working status. 
* Trace width for all circuit has been modified according to its functionality. 

* * * * * * * * * * * * * * * * * * * * * * * * * * * * * * * * * * * * *

> Next Stage
* Waiting for further notifying.

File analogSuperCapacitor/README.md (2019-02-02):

# Passive Super-Capacitor Design
In order to be able to used more than 80W of power at any instatianious time, a super-capacitor bank is needed to "smooth" the power draw.

## Usage

First download or clone `Passive Super-Capacitor Design`:

Open Kicad and open the Kicad project file.
```sh
rm_supercap.pro
```

Once selected the project should be loaded and ready to view or edit!

## Todo

1. Update `README.md`
2. Update board design:
3. Make bill of materials (BOM)
4. Upload SPICE files

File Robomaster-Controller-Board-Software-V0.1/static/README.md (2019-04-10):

Files in `data/` will be uploaded to esp32 using [this](https://github.com/me-no-dev/arduino-esp32fs-plugin).

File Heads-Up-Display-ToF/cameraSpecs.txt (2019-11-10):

Robomaster Video Transmitter Module

	Resolution: 1280 x 720	
	Framerate: 60 Hz

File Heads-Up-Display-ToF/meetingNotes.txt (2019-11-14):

TODO 11/9

 Github
  - Add documentation

 OLED
  - Leave spi holes, dont solder pins into them
  - DONE Add Logo to the back of the board
  - DONE Try and change resistors to get up to 12v current voltage recorder was 11.67v
    - Calculation with current resistors is 11.74, so nothing wrong with design. Changing 5.6k resistor to 5.3k will get voltage up to 12.33v
    - Test current board with power supply at 11.67 to see if it works

 Ammo Board
  - DONE Get rid of xt30, use 2 pin jst
  - DONE Test ammo sensor for 7 inches
  - Photo detector can detect up to 7 inches, but voltage needs to be at 1.7 and pulls 340 mA, so buck cant handle two of them (maybe switch to just one detector)

TODO 11/1

  - DONE Test control board (Seems to work, will do more thourough test later, although without the bootloader only power can be tested)

  - DONE Test ammo sensors (test successful, photoresistor has large fov, so a cover might be a good idea to block IR from other sources)

  - DONE Decide whether to receive 12 volt or 3.3 volt for the control board (we will recieve 3.3v)

  - DONE Add 5v to 3.3v buck converter (measure power consumption of the HUD control board)

  - DONE Add spi pins on board so that the bootloader can be burned onto the board

  - Make ring outline for the ammo detector

  - DONE Camera position changed, let dansen know

Ammo Indicator
  - Can use mux 8 to 3 or GPIO expander to take all photogate sensor outputs and condense it to less pins / data (dont need mux because only 2 photoresistors)

  - Need logic amplifier (don't need)

  - IR beam break sensor OR Photodetector logic output (latter)

  - PLPVQ Diode (Kevin sent it) for the laser, find photodetector that can sense it 

  - Seperate PCB for indicators, take 24V from slip ring and step down to 1.5V (Use XT30 right angle connectors for the high voltage)

Notes from Meeting (10/26)

  - Find own regulators to step down the voltage (buck converter may not work)

Feedback for OLEDBoard (10/16)

  - DONE Check logic voltage levels on all logic lines, (check if CH340 can take 5v logic when powered by 3.3V (check if it has level shifting)

  - DONE Remove XT30 for the ammo board (it will be powered by new power distro)

  - DONE Add ground to all connectors (including ammo gpio)

  - DONE remove unnecessory pins for connectors

Notes from Meeting (10/12)

Control Board Code
  - Use software I2C to mimic another I2C line so that the oled wont slow us down

  - OLED will be right in front of camera, so  smaller HUD elements will be used (make sure not to get blocked by the dji hud elements)

Control Board

  - DONE Get button from kevin

  - DONE Add 3.3V capacitor group from the boost under the atmega

  - DONE Copy sparkfun's schematic for a usb c to serial converter, so change micro usb to usb c

  - DONE Add 2 XT30 power connectors to power the control board and to output power to the ammo indicator

  - DONE Resonators must have same length for both in and out wires

  - DONE Move boost away from ATMEGA328

  - NO Use same hole dimensions and placement as the sparkfun OLED board (might change)

Notes from Meeting (10/7)

  OLED Board
  - DONE Add mounting holes from what kevin sent you (you have to add it as a symbol)

  - DONE Change liquid crystal to surface mount and have it and the capacitors next to it closer to the atmega DONE (no more capacitors because it is a resonator)

  - DONE Use 0603 size for all capacitors and resistors

  - DONE Use the specified layout on the boost converter datasheet or copy from the sparkfun board (do this)

  - DONE Change connector to the one kevin sent you

  - DONE Change options to vcc or gronund depending on which side of resistor they are on

  - DONE Add reset button on the atmega

  - DONE Add pullup resistor for the I2C (1K)

  - DONE More space efficiency (Rotate boost and shove it in the corner)

  - CS can run on the bottom under the atmega

  - DONE Include on-board usb c programmer using sparkfun avr programmer and changing the mini usb to micro usb with the usb c breakout from sparkfun

  - DONE Add 3 pin connector for the ammo indecator system (GPIO Connection)

  Tof Code
  - Do not make wall direction relative to gimbal view, add where the front of the robot is currently relative to the gimbal

  Ammo Indicator
  - Can use mux 8 to 3 or GPIO expander to take all photogate sensor outputs and condense it to less pins / data

  - IR beam break sensor OR Photodetector logic output (latter)

  - PLPVQ Diode (Kevin sent it) for the laser, find photodetector that can sense it 

  - Seperate PCB for indicators, take 24V from slip ring and step down to 1.5V (Use XT30 right angle connectors for the high voltage)

  Orientation
  - The data for the orientation can be an int from 0 to 8 that gives a general direction

  Communication
  - Create struct for the data that is being sent to the board

Notes from Meeting (9/28)

 - HUD will be seperate from main control board. So either make the HUD work with STM32 (HUD library is very big so that will be difficult) or create a pcb board for the HUD with an onboard microcontroller (arduino) that will read the UART package and take the apropriate data

 - Robot needs to be able  to navigate through a tunnel so 2 ToF sensors on the front and back will be needed so that the robot does not run into a wall. The two on the side will still be there, bringing the total number of ToF sensors to 6.

 - FPV camera from china is still not here so buying a similar one to test the HUD will be the best. FPV camera stats should be in the referee system manual, find one that is similar and buy it.

 - Still no extra control board for testing, need more breadboards and jumper wire.

 - Seperate code for ToF sensors on engineer robot. 2 sensors on the front of the robot to determine if the robot is perpendicular to the platform that the ammo is on top oof. 2 more to determine if the grabber arms are in between the ammo box and wont hit it when the arms drop down. Maybe 2 more to detect if the box is inbetween the two arms after the arms drop down.

 - Be able to see feedback for enemy hit or their health. Enemy health data can be gathered from the referee system. When the robot shoots a ball, see if any of the health values of the enemy robots change.

 - Refresh rate for HUD info: 50Hz (Take average of last 5 ToF readings, so interrupt is at 250 Hz

 - OLED will be small part of FPV camera feed, so make all HUD elements big and noticible

 - Get DGI Hud so that we don't cover an element of the HUD

 - Investigate sparkfun functions for sending data to the OLED and see if we can get the display to work without it

 - Find solution for when the ammo is low and displaying that to the HUD (detect is balls are within a certain plane)
 	- Have 2 PCBs with photogate emmiters on one side and photogate recievers on the other, have LEDs that light up when there is something in the way so that it can be calibrated

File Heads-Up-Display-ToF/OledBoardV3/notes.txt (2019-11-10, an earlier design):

Custom OLED Board
	Microcontroller: ATMEGA328p TQFP
	Communication Requirments
	- Read UART
	- Send I2C

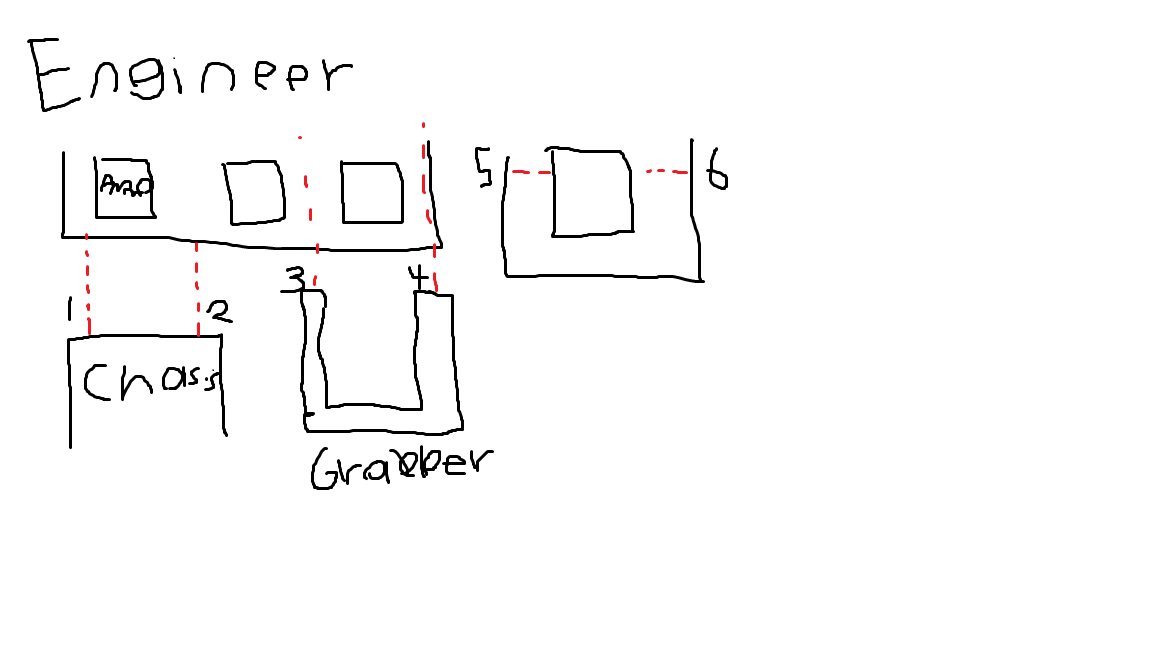
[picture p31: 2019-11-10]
Heads-Up-Display-ToF/DesignConcepts/EngineerToFConcept(9-28).png

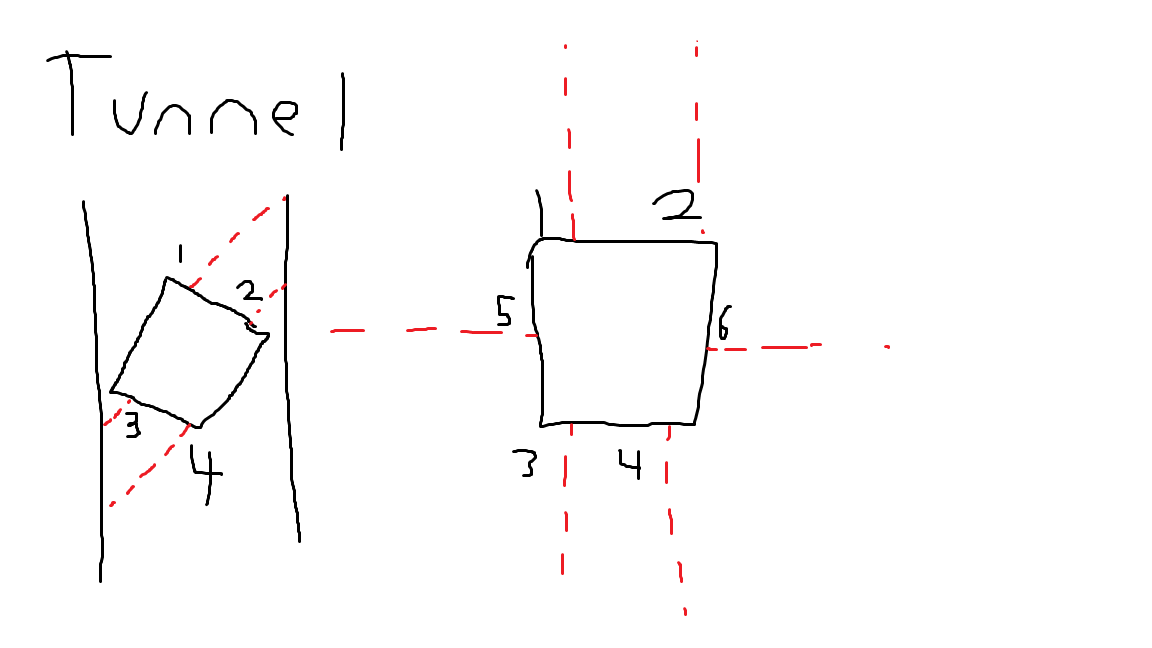
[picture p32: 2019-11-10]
Heads-Up-Display-ToF/DesignConcepts/StandardToFConcept.png

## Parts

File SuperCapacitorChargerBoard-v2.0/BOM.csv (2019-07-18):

Part | Value | Device | Package | Description | AVAILABILITY | BOM | DESCRIPTION | MF | MP | MPN | OC_NEWARK | PACKAGE | PART_# | PRICE | PROD_ID | SF_ID | SPICEPREFIX | VALUE
BW_SEL_HIGHT_RES |  | SOLDERJUMPER | SOLDERJUMPER_ARROW_NOPASTE | SMD Solder JUMPER |  | EXCLUDE
C1 | 0.1uF | 0.1UF-0603-25V-(+80/-20%) | 0603 | 0.1µF ceramic capacitors |  |  |  |  |  |  |  |  |  |  | CAP-00810 |  |  | 0.1uF
C2 | 4.7uF | 0.1UF-0603-25V-(+80/-20%) | 0603 | 0.1µF ceramic capacitors |  |  |  |  |  |  |  |  |  |  | CAP-00810 |  |  | 0.1uF
C3 | 0.1uF | 0.1UF-0603-25V-(+80/-20%) | 0603 | 0.1µF ceramic capacitors |  |  |  |  |  |  |  |  |  |  | CAP-00810 |  |  | 0.1uF
C4 | 0.1uF | 0.1UF-0603-25V-(+80/-20%) | 0603 | 0.1µF ceramic capacitors |  |  |  |  |  |  |  |  |  |  | CAP-00810 |  |  | 0.1uF
C5 | 0.1uF | 0.1UF-0603-25V-(+80/-20%) | 0603 | 0.1µF ceramic capacitors |  |  |  |  |  |  |  |  |  |  | CAP-00810 |  |  | 0.1uF
C6 | 0.1uF | 0.1UF-0603-25V-(+80/-20%) | 0603 | 0.1µF ceramic capacitors |  |  |  |  |  |  |  |  |  |  | CAP-00810 |  |  | 0.1uF
C7 | 0.1uF | 0.1UF-0603-25V-(+80/-20%) | 0603 | 0.1µF ceramic capacitors |  |  |  |  |  |  |  |  |  |  | CAP-00810 |  |  | 0.1uF
C8 | 4.7uF | 4.7UF-1206-16V-(+80/-20%) | 1206 | 4.7µF ceramic capacitors |  |  |  |  |  |  |  |  |  |  | CAP-10300 |  |  | 4.7uF
C9 | 4.7uF | 4.7UF-1206-16V-(+80/-20%) | 1206 | 4.7µF ceramic capacitors |  |  |  |  |  |  |  |  |  |  | CAP-10300 |  |  | 4.7uF
C10 | 0.1uF | 0.1UF-0603-25V-(+80/-20%) | 0603 | 0.1µF ceramic capacitors |  |  |  |  |  |  |  |  |  |  | CAP-00810 |  |  | 0.1uF
C11 | 0.1uF | 0.1UF-0603-25V-(+80/-20%) | 0603 | 0.1µF ceramic capacitors |  |  |  |  |  |  |  |  |  |  | CAP-00810 |  |  | 0.1uF
C12 | 22p | CAP0603-CAP | 0603-CAP | Capacitor |  |  |  |  |  |  | unknown
C13 | 22p | CAP0603-CAP | 0603-CAP | Capacitor |  |  |  |  |  |  | unknown
C14 | 0.1uF | 0.1UF-0603-25V-(+80/-20%) | 0603 | 0.1µF ceramic capacitors |  |  |  |  |  |  |  |  |  |  | CAP-00810 |  |  | 0.1uF
C15 | 0.1uF | 0.1UF-0603-25V-(+80/-20%) | 0603 | 0.1µF ceramic capacitors |  |  |  |  |  |  |  |  |  |  | CAP-00810 |  |  | 0.1uF
C16 | 1nF | 1.0NF/1000PF-0603-50V-10% | 0603 | 1nF/1,000pF ceramic capacitors |  |  |  |  |  |  |  |  |  |  | CAP-07886 |  |  | 1nF
C17 | 0.1uF | 0.1UF-0603-25V-(+80/-20%) | 0603 | 0.1µF ceramic capacitors |  |  |  |  |  |  |  |  |  |  | CAP-00810 |  |  | 0.1uF
C18 | 0.1uF | 0.1UF-0603-25V-(+80/-20%) | 0603 | 0.1µF ceramic capacitors |  |  |  |  |  |  |  |  |  |  | CAP-00810 |  |  | 0.1uF
C19 | 0.1uF | 0.1UF-0603-25V-(+80/-20%) | 0603 | 0.1µF ceramic capacitors |  |  |  |  |  |  |  |  |  |  | CAP-00810 |  |  | 0.1uF
C20 | 1nF | 1.0NF/1000PF-0603-50V-10% | 0603 | 1nF/1,000pF ceramic capacitors |  |  |  |  |  |  |  |  |  |  | CAP-07886 |  |  | 1nF
C21 | 4.7uF | 4.7UF-1206-16V-(+80/-20%) | 1206 | 4.7µF ceramic capacitors |  |  |  |  |  |  |  |  |  |  | CAP-10300 |  |  | 4.7uF
C22 | 4.7uF | 4.7UF-1206-16V-(+80/-20%) | 1206 | 4.7µF ceramic capacitors |  |  |  |  |  |  |  |  |  |  | CAP-10300 |  |  | 4.7uF
C23 | 0.1uF | 0.1UF-0603-25V-(+80/-20%) | 0603 | 0.1µF ceramic capacitors |  |  |  |  |  |  |  |  |  |  | CAP-00810 |  |  | 0.1uF
C24 | 0.1uF | 0.1UF-0603-25V-(+80/-20%) | 0603 | 0.1µF ceramic capacitors |  |  |  |  |  |  |  |  |  |  | CAP-00810 |  |  | 0.1uF
C25 | 4.7uF | 4.7UF-1206-16V-(+80/-20%) | 1206 | 4.7µF ceramic capacitors |  |  |  |  |  |  |  |  |  |  | CAP-10300 |  |  | 4.7uF
C26 | 0.1uF | 0.1UF-0603-25V-(+80/-20%) | 0603 | 0.1µF ceramic capacitors |  |  |  |  |  |  |  |  |  |  | CAP-00810 |  |  | 0.1uF
C27 | 4.7uF | 4.7UF-1206-16V-(+80/-20%) | 1206 | 4.7µF ceramic capacitors |  |  |  |  |  |  |  |  |  |  | CAP-10300 |  |  | 4.7uF
C28 | 4.7uF | 4.7UF-1206-16V-(+80/-20%) | 1206 | 4.7µF ceramic capacitors |  |  |  |  |  |  |  |  |  |  | CAP-10300 |  |  | 4.7uF
C29 | 4.7uF | 4.7UF-1206-16V-(+80/-20%) | 1206 | 4.7µF ceramic capacitors |  |  |  |  |  |  |  |  |  |  | CAP-10300 |  |  | 4.7uF
C30 | 4.7uF | 4.7UF-1206-16V-(+80/-20%) | 1206 | 4.7µF ceramic capacitors |  |  |  |  |  |  |  |  |  |  | CAP-10300 |  |  | 4.7uF
C31 | 4.7uF | 4.7UF-1206-16V-(+80/-20%) | 1206 | 4.7µF ceramic capacitors |  |  |  |  |  |  |  |  |  |  | CAP-10300 |  |  | 4.7uF
C32 | 0.1uF | 0.1UF-0603-25V-(+80/-20%) | 0603 | 0.1µF ceramic capacitors |  |  |  |  |  |  |  |  |  |  | CAP-00810 |  |  | 0.1uF
C33 | 1nF | 1.0NF/1000PF-0603-50V-10% | 0603 | 1nF/1,000pF ceramic capacitors |  |  |  |  |  |  |  |  |  |  | CAP-07886 |  |  | 1nF
C34 | 22uF | 4.7UF-1206-16V-(+80/-20%) | 1206 | 4.7µF ceramic capacitors |  |  |  |  |  |  |  |  |  |  | CAP-10300 |  |  | 4.7uF
C35 | 22uF | 4.7UF-1206-16V-(+80/-20%) | 1206 | 4.7µF ceramic capacitors |  |  |  |  |  |  |  |  |  |  | CAP-10300 |  |  | 4.7uF
C36 | 22uF | 4.7UF-1206-16V-(+80/-20%) | 1206 | 4.7µF ceramic capacitors |  |  |  |  |  |  |  |  |  |  | CAP-10300 |  |  | 4.7uF
C37 | 22uF | 4.7UF-1206-16V-(+80/-20%) | 1206 | 4.7µF ceramic capacitors |  |  |  |  |  |  |  |  |  |  | CAP-10300 |  |  | 4.7uF
C38 | 22uF | 4.7UF-1206-16V-(+80/-20%) | 1206 | 4.7µF ceramic capacitors |  |  |  |  |  |  |  |  |  |  | CAP-10300 |  |  | 4.7uF
C39 | 22uF | 4.7UF-1206-16V-(+80/-20%) | 1206 | 4.7µF ceramic capacitors |  |  |  |  |  |  |  |  |  |  | CAP-10300 |  |  | 4.7uF
C40 | 4.7uF | 4.7UF-1206-16V-(+80/-20%) | 1206 | 4.7µF ceramic capacitors |  |  |  |  |  |  |  |  |  |  | CAP-10300 |  |  | 4.7uF
C41 | 0.1uF | 0.1UF-0603-25V-(+80/-20%) | 0603 | 0.1µF ceramic capacitors |  |  |  |  |  |  |  |  |  |  | CAP-00810 |  |  | 0.1uF
CAP_CHARGING_CURRENT | ACS723 | ACS723 | SO08 |  |  |  |  |  |  |  |  |  | ACS723ACS723LLCTR-05AB-T2 |  | IC-13872
D1 | 3A/40V/500mV | DIODE-SCHOTTKY-B340A | SMA-DIODE | Schottky diode |  |  |  |  |  |  |  |  |  |  | DIO-09886 |  |  | 3A/40V/500mV
D2 | RED | LED-RED0603 | LED-0603 | Red SMD LED |  |  |  |  |  |  |  |  |  |  | DIO-00819 |  |  | RED
D3 | GREEN | LED-GREEN0603 | LED-0603 | Green SMD LED |  |  |  |  |  |  |  |  |  |  | DIO-00821 |  |  | GREEN
D4 | MMSZ5242/12v | DIODE-ZENER-MMSZ5232BS | SOD-323 | Zener Diode |  |  |  |  |  |  |  |  |  |  | DIO-12442 |  |  | 5.6V
D5 | 3A/40V/500mV | DIODE-SCHOTTKY-B340A | SMA-DIODE | Schottky diode |  |  |  |  |  |  |  |  |  |  | DIO-09886 |  |  | 3A/40V/500mV
D6 | 1N4148WS | 1N4148WS | SOD323 | http://octopart.com/1n4148ws-fairchild+semiconductor-7851016 | Unavailable |  | Diode Switching 75V 0.3A 2-Pin SOD-323 T/R | ON Semiconductor | 1N4148WS |  |  | S-0 Good-Ark |  | None
D7 | 1N4148WS | 1N4148WS | SOD323 | http://octopart.com/1n4148ws-fairchild+semiconductor-7851016 | Unavailable |  | Diode Switching 75V 0.3A 2-Pin SOD-323 T/R | ON Semiconductor | 1N4148WS |  |  | S-0 Good-Ark |  | None
FB1 | 600Ω/1.8A | FERRITE_BEAD-0603 | 0603 | Ferrite Bead (blocks, cores, rings, chokes, etc.) |  |  |  |  |  |  |  |  |  |  | NDUC-13805 |  |  | 30Ω/1.8A
H_MOS | BSC018N04 | BSC018N04 | TRANS_BSC076N06NS3-G
L1 | SWPA3012S4R7MT | L-USL3230M | L3230M | INDUCTOR, American symbol |  |  |  |  |  |  |  |  |  |  |  |  | L
L2 | SWPA3012S4R7MT | L-USL3230M | L3230M | INDUCTOR, American symbol |  |  |  |  |  |  |  |  |  |  |  |  | L
L3 | WHC1265-10UH | WHC1265-10UH | WHC1265-10UH
LM5050 | LM5050 | LM5050 | TSOT-23-6-SOT-23-6
L_MOS | BSC018N04 | BSC018N04 | TRANS_BSC076N06NS3-G
MOSFEL1 | BSC018N04 | BSC018N04 | TRANS_BSC076N06NS3-G
MOTOR_MOS | IRF4905S | IRF4905S | D2PAK
MP2451 | MP2451 | MP2451 | TSOT-23-6-SOT-23-6
MP2451(2) | MP2451 | MP2451 | TSOT-23-6-SOT-23-6
MTR_OUT_CURRENT1 | ACS723 | ACS723 | SO08 |  |  |  |  |  |  |  |  |  | ACS723ACS723LLCTR-05AB-T2 |  | IC-13872
PROGRAMMER | BM04B-GHS-TBT | BM04B-GHS-TBT | BM04B-GHS-TBT
Q1 | S8050/25v 500mW | TRANS_NPN-MMBT2222AL | SOT23-3 | NPN transistor |  |  |  |  |  |  |  |  |  |  | TRANS-08049 |  |  | 600mA/40V
Q2 | NPN | TRANSISTOR_NPNSOT23-3 | SOT23-3 | Transistor NPN
Q3 | NPN | TRANSISTOR_NPNSOT23-3 | SOT23-3 | Transistor NPN
R1 | 10K | RESISTOR0603 | 0603 | Generic Resistor Package
R2 | 10K | RESISTOR0603 | 0603 | Generic Resistor Package
R3 | 100K | RESISTOR0603 | 0603 | Generic Resistor Package
R4 | 124K | RESISTOR0603 | 0603 | Generic Resistor Package
R5 | 40.2k | RESISTOR0603 | 0603 | Generic Resistor Package
R6 | 16.2k | RESISTOR0603 | 0603 | Generic Resistor Package
R7 | 1.69k | RESISTOR0603 | 0603 | Generic Resistor Package
R8 | 16.2k | RESISTOR0603 | 0603 | Generic Resistor Package
R9 | 1.69k | RESISTOR0603 | 0603 | Generic Resistor Package
R10 | 16.2k | RESISTOR0603 | 0603 | Generic Resistor Package
R11 | 1.69k | RESISTOR0603 | 0603 | Generic Resistor Package
R12 | 1k | RESISTOR0603 | 0603 | Generic Resistor Package
R13 | 1k | RESISTOR0603 | 0603 | Generic Resistor Package
R14 | 100 | RESISTOR0603 | 0603 | Generic Resistor Package
R15 | 10k | RESISTOR0603 | 0603 | Generic Resistor Package
R16 | 100 | RESISTOR0603 | 0603 | Generic Resistor Package
R17 | 100K | RESISTOR0603 | 0603 | Generic Resistor Package
R18 | 124K | RESISTOR0603 | 0603 | Generic Resistor Package
R19 | 8.87k | RESISTOR0603 | 0603 | Generic Resistor Package
R20 | 470 | RESISTOR0603 | 0603 | Generic Resistor Package
R21 | 470 | RESISTOR0603 | 0603 | Generic Resistor Package
R22 | 220 | RESISTOR0603 | 0603 | Generic Resistor Package
R23 | 220 | RESISTOR0603 | 0603 | Generic Resistor Package
R24 | 10K | RESISTOR0402 | C0402 | Resistor
R25 | 10K | RESISTOR0402 | C0402 | Resistor
R26 | 10K | RESISTOR0402 | C0402 | Resistor
R27 | 10K | RESISTOR0402 | C0402 | Resistor
TOTAL_BAT_CURRENT | ACS723 | ACS723 | SO08 |  |  |  |  |  |  |  |  |  | ACS723ACS723LLCTR-05AB-T2 |  | IC-13872
TO_BAT | XT60PW-M | XT60PW-M | AMASS_XT60PW-M |  | Unavailable |  |  | AMASS | XT60PW-M |  |  | Package Analog Devices |  | None
TO_CAP | XT60PW-M | XT60PW-M | AMASS_XT60PW-M |  | Unavailable |  |  | AMASS | XT60PW-M |  |  | Package Analog Devices |  | None
TO_MOTOR | XT60PW-M | XT60PW-M | AMASS_XT60PW-M |  | Unavailable |  |  | AMASS | XT60PW-M |  |  | Package Analog Devices |  | None
U$1 | STM32F334K8T | STM32F334K8T | QFP80P900X900X160-32N
U$6 | MP1907GQ-Z | MP1907GQ-Z | QFN10
U1 | DUAL-OPTOISOLATOR_SOIC8 | DUAL-OPTOISOLATOR_SOIC8 | SO08 | Optocoupler, Phototransistor Output, Dual Channel |  |  |  |  |  |  |  |  |  |  | IC-09076
USART | S3B-PH-SM4_TB | S3B-PH-SM4_TB | S3B-PH-SM4_TB
Y1 | 16MHz | CRYSTAL-16MHZSMD-5X3.2 | CRYSTAL-SMD-5X3.2-4PAD | 16MHz Crystal |  |  |  |  |  |  |  |  |  |  | XTAL-08218 | COM-00094 |  | 16MHz

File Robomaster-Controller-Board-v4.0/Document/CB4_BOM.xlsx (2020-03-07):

Qty | Value | Device | Package | Links | Parts | Description | AVAILABILITY | DESCRIPTION.1 | HEIGHT | MANUFACTURER_NAME | MANUFACTURER_PART_NUMBER | MF | MOUSER_PART_NUMBER | MOUSER_PRICE-STOCK | MP | PACKAGE.1 | POPULARITY | PRICE | PROD_ID | RS_PART_NUMBER | RS_PRICE-STOCK | SPICEPREFIX | VALUE.1 | Column1
2 | 10k | 1KOHM-ARRAY(4)-0805_ARV-1/10W-5% | 0805-ARV |  | RN1, RN2 | 4 x 1kÎ© resistor array |  |  |  |  |  |  |  |  |  |  |  |  | RES-13020 |  |  |  | 1k
1 | 40.2K | 220KOHM-0603-1/10W-1% | 0603 | https://www.digikey.com/product-detail/en/stackpole-electronics-inc/RMCF0603FT40K2/RMCF0603FT40K2CT-ND/1943095 | R7 | 220kÎ© resistor |  |  |  |  |  |  |  |  |  |  |  |  | RES-08969 |  |  |  | 220k
1 | BM03-GHS_TBT | BM03-GHS_TBT | BM03-GHS-TBT |  | AMMO_DETEC
1 | 100nF | CAP_CERAMIC0603_NO | 0603-NO | https://www.digikey.com/product-detail/en/kemet/C0603C104Z3VACTU/399-1100-1-ND/411375 | C26 | Ceramic Capacitors
7 | 10uF | CAP_CERAMIC0603_NO | 0603-NO | https://www.digikey.com/product-detail/en/murata-electronics/GRM188R61A106KE69J/490-14372-1-ND/6606833 | C7, C9, C10 | Ceramic Capacitors
6 | 1uF | CAP_CERAMIC0603_NO | 0603-NO | https://www.digikey.com/product-detail/en/samsung-electro-mechanics/CL10A105KP8NNNC/1276-1182-1-ND/3889268 | C5, C6, C8, C11, C12, C13, C14, C16 | Ceramic Capacitors
4 | 22pF | CAP_CERAMIC0603_NO | 0603-NO | https://www.digikey.com/product-detail/en/%E5%9E%88%ED%9B%87/CC0603JRNPO8BN220/311-3952-1-ND/8025041 | C17, C23, C24, C25 | Ceramic Capacitors
1 | 47nF | CAP_CERAMIC0603_NO | 0603-NO | https://www.digikey.com/product-detail/en/%E5%9E%88%ED%9B%87/CC0603KRX5R8BB474/311-3365-1-ND/6818335 | C15 | Ceramic Capacitors
3 | 0.1uF | C-EUC0603 | C0603 | https://www.digikey.com/product-detail/en/kemet/C0603C104Z3VACTU/399-1100-1-ND/411375 | C2, C18, C22 | CAPACITOR, European symbol |  |  |  |  |  |  |  |  |  |  | 73 |  |  |  |  | C
1 | 12mhz | CRYSTAL2.5X2.0 | CRYSTAL_2.5X2 | https://www.digikey.com/product-detail/en/ndk-america-inc/NX3215SA-32.768K-STD-MUA-8/644-1156-1-ND/2261473 | Y2 | Crystals
1 | 150p | C-USC0603 | C0603 | https://www.digikey.com/product-detail/en/kemet/C0603C151J5GACTU/399-1063-1-ND/411338 | C3 | CAPACITOR, American symbol
1 | o | C-USC1206 | C1206 | https://www.digikey.com/product-detail/en/murata-electronics/GRM188R60J226MEA0D/490-7611-1-ND/4280544 | C1 | CAPACITOR, American symbol
1 | MBR054 | DIODE-SCHOTTKYSOD-123 | SOD-123 | https://www.digikey.com/product-detail/en/micro-commercial-co/MBR0540-TP/MBR0540TPMSCT-ND/717367 | D5
1 | ferrite | FERRITE-0805NO | 0805-NO@1 | https://www.digikey.com/product-detail/en/taiyo-yuden/BKP2125HS600-T/587-1932-1-ND/1465402 | FB1 | Ferrite Bead
4 | G3VM-61VY2 | G3VM-61VY2 | SOP254P700X230-4N | https://www.digikey.com/product-detail/en/omron-electronics-inc-emc-div/G3VM-61VY2-TR05/Z6068CT-ND/6207087 | SSR1, SSR2, SSR3, SSR4 | Solid State Relays - PCB Mount Mos Fet Relay, SMT 60V, 1 form A,SOP4 |  | Solid State Relays - PCB Mount Mos Fet Relay, SMT 60V, 1 form A,SOP4 | 2.3mm | Omron Electronics | G3VM-61VY2 |  | 653-G3VM61VY2 | https://www.mouser.com/Search/Refine.aspx?Keyword=653-G3VM61VY2
1 |  | JTAG-CORTEX | 2X05_1.27MM_SMT | https://www.digikey.com/product-detail/en/cnc-tech/3220-10-0100-00/1175-1627-ND/3883661 | PROGRAMMER | Serial Wire (SW-DP) Connector
2 | GREEN | LEDCHIPLED_0603 | CHIPLED_0603 | https://www.digikey.com/product-detail/en/kingbright/APT1608SGC/754-1121-1-ND/1747838 | PC1, POW | LED
2 | RED | LEDCHIPLED_0603 | CHIPLED_0603 | https://www.digikey.com/product-detail/en/kingbright/APT1608EC/754-1117-1-ND/1747834 | PC1, POW | LED
1 | LSM6DS33 | LSM6DS33 | LGA16_3X3MM | https://www.digikey.com/product-detail/en/stmicroelectronics/LSM6DS33TR/497-15996-1-ND/5452396 | IMU
1 | 4.7u | MHCI0603-4R7M-R8 | MHCI0603-4R7M-R8 | https://www.digikey.com/product-detail/en/taiyo-yuden/MBKK1608T4R7M/587-4152-1-ND/5035312 | L2
1 |  | MICROSD | MICROSD |  | X8 | MicroSD/Transflash Card Holder with SPI pinout
1 | 3.1A/30V/105mÎ© | MOSFET_PCH-DMG2307L | SOT23-3 |  | Q1 | P-channel MOSFETs |  |  |  |  |  |  |  |  |  |  |  |  | TRANS-11308 |  |  |  | 3.1A/30V/105mÎ©
1 | MP1584_V2 | MP1584_V2 | MP1584_V2 | https://www.digikey.com/product-detail/en/monolithic-power-systems-inc/MP1584EN-LF-Z/1589-1533-1-ND/9433299 | U$10
1 |  | NRF51822_MODULE_MDBT40 | BLE_MODULE_RAYTAC_MDBT40 | https://www.digikey.com/product-detail/en/nordic-semiconductor-asa/NRF51822-QFAC-R7/1490-1049-1-ND/5125206 | U1 | nRF51822 Bluetooth Low Energy Module
1 | PESD1CAN | PESD1CAN | SOT23-3 | https://www.digikey.com/product-detail/en/nexperia-usa-inc/PESD1CAN-UX/1727-1306-1-ND/4386316 | D2 | PESD1CAN is used to protect two automotive CAN bus lines from ESD. | Unavailable | 50V Clamp 3A _8/20Âµs_ Ipp Tvs Diode Surface Mount SC-70 |  |  |  | NXP Semiconductors |  |  | PESD1CAN | SC-70 NXP Semiconductors |  | None
1 | 125K->127K | RESISTOR0603 | 0603 | https://www.digikey.com/product-detail/en/te-connectivity-passive-product/RQ73C1J127KBTD/A140155CT-ND/9481642 | R8 | Generic Resistor Package
6 | 100k | R-US_R0603 | R0603 | https://www.digikey.com/product-detail/en/bourns-inc/CR0603-JW-104ELF/CR0603-JW-104ELFCT-ND/3767631 | R4, R5, REFF1 | RESISTOR, American symbol
3 | 10K | R-US_R0603 | R0603 | https://www.digikey.com/product-detail/en/bourns-inc/CR0603-JW-103ELF/CR0603-JW-103ELFCT-ND/3592890 | R1, R2, R20 | RESISTOR, American symbol |  |  |  |  |  |  |  |  |  |  | 77 |  |  |  |  | R
2 | 1K | R-US_R0603 | R0603 | https://www.digikey.com/product-detail/en/stackpole-electronics-inc/RNCS0603BKE1K00/RNCS0603BKE1K00CT-ND/1800114 | R9, R10 | RESISTOR, American symbol |  |  |  |  |  |  |  |  |  |  | 77 |  |  |  |  | R
2 | 2.2K | R-US_R0603 | R0603 | https://www.digikey.com/product-detail/en/stackpole-electronics-inc/RMCF0603JT2K20/RMCF0603JT2K20CT-ND/1943178 | R12, R27 | RESISTOR, American symbol |  |  |  |  |  |  |  |  |  |  | 77 |  |  |  |  | R
1 | 24k | R-US_R0603 | R0603 | https://www.digikey.com/product-detail/en/stackpole-electronics-inc/RMCF0603FT24K0/RMCF0603FT24K0CT-ND/7790168 | R6 | RESISTOR, American symbol
1 | 2K | R-US_R0603 | R0603 | https://www.digikey.com/product-detail/en/stackpole-electronics-inc/RMCF0603FT24K0/RMCF0603FT24K0CT-ND/7790168 | R14 | RESISTOR, American symbol |  |  |  |  |  |  |  |  |  |  | 77 |  |  |  |  | R
1 | 4.7K | R-US_R0603 | R0603 | https://www.digikey.com/products/en/resistors/chip-resistor-surface-mount/52?k=resistor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 | R24 | RESISTOR, American symbol
2 | 5.1K | R-US_R0603 | R0603 | https://www.digikey.com/product-detail/en/stackpole-electronics-inc/RMCF0603JT5K10/RMCF0603JT5K10CT-ND/1943185 | R17, R18 | RESISTOR, American symbol |  |  |  |  |  |  |  |  |  |  | 77 |  |  |  |  | R
2 | 60->60.4 | R-US_R0603 | R0603 | https://www.digikey.com/product-detail/en/stackpole-electronics-inc/RMCF0603FT60K4/RMCF0603FT60K4CT-ND/1943106 | R25, R26 | RESISTOR, American symbol
5 | S2B-PH-SM4_TB | S2B-PH-SM4_TB | S2B-PH-SM4_TB | https://www.digikey.com/product-detail/en/jst-sales-america-inc/S2B-PH-SM4-TB-LF-SN/455-1749-1-ND/926846 | AUX_GPIO2, RELAY1, RELAY2, RELAY3, RELAY4
2 | S2B-ZR-SM4A-TF(LF)(SN) | S2B-ZR-SM4A-TF(LF)(SN) | JST_S2B-ZR-SM4A-TF(LF)(SN) | https://www.digikey.com/product-detail/en/jst-sales-america-inc/S2B-ZR-SM4A-TF-LF-SN/455-1693-1-ND/926820 | CANBUS, CANBUS1 | ZH Series 2 Position 1.5 mm Pitch Surface Mount Side Entry Shrouded Header | Unavailable | Connector Header Surface Mount, Right Angle 2 position 0.059 _1.50mm_ |  |  |  | JST Sales |  |  | S2B-ZR-SM4A-TF_LF__SN_ | None |  | None
2 | S3B-PH-SM4_TB | S3B-PH-SM4_TB | S3B-PH-SM4_TB | https://www.digikey.com/product-detail/en/jst-sales-america-inc/S3B-PH-SM4-TB-LF-SN/455-1750-1-ND/926847 | MAIN_BOARD, SWITCH
1 | S4B-PH-SM4_TB | S4B-PH-SM4_TB | S4B-PH-SM4_TB | https://www.digikey.com/product-detail/en/jst-sales-america-inc/S4B-PH-SM4-TB-LF-SN/455-1751-1-ND/926848 | VISION
6 | SM04B-GHS-TB(LF)(SN)- | SM04B-GHS-TB(LF)(SN)- | JST_SM04B-GHS-TB(LF)(SN)- | https://www.digikey.com/product-detail/en/jst-sales-america-inc/SM04B-GHS-TB-LF-SN/455-1566-1-ND/807834 | I2C_1, I2C_2, I2C_3, I2C_4, I2C_5, I2C_6 | Conn Header Gh Side 4pos 1.25mm | Unavailable | Connector Header Surface Mount, Right Angle 4 position 0.049 _1.25mm_ |  |  |  | JST Sales |  |  | SM04B-GHS-TB_LF__SN_- | None |  | None
1 | SMD-DIODE-SCHOTTKY-40V-3A(DO-214AB) | SMD-DIODE-SCHOTTKY-40V-3A(DO-214AB) | DO-214AB | kevin got it | D3 | 304020018 | Unavailable | Rectifier, Schottky | DO-214AB | 3.0A IF | 0.75V | 40V | 100A IFRM | 10000V/us | 1000pF |  |  |  | Vishay |  |  | SS34-E3/57T | DO-214 Vishay
1 | 25Q16 | SPIFLASH_8PIN | SOIC8_150MIL | https://www.digikey.com/product-detail/en/winbond-electronics/W25Q16JVSSIQ/W25Q16JVSSIQ-ND/6193769 | SPI_FLASH | SOIC8 SPI Flash
1 | STEMMA_I2C_QT | STEMMA_I2C_QT | JST_SH4 |  | QWIIC
1 | STM32F405R | STM32F405R | TQFP64 | https://www.digikey.com/product-detail/en/stmicroelectronics/STM32F405RGT6TR/497-17432-1-ND/8024114 | STM32F405RGTX | STM32F405 64 pin LQFP
1 | EG1319 | SWITCH_DPDTEG1390 | EG1390 | kevin gonna replace | SW1 | Switch - DPDT
1 | KMR2 | SWITCH_TACT_SMT4.6X2.8 | BTN_KMR2_4.6X2.8 | https://www.digikey.com/product-detail/en/c-k/KMR221GLFS/401-1427-1-ND/550466 | RESET | SMT Tact Switches
1 | TJA1050 | TJA1050 | SOT96-1 | https://www.digikey.com/product-detail/en/nxp-usa-inc/TJA1050T-CM-118/568-10292-1-ND/4162437 | CAN_CONVERTER | High speed CAN transceiver | Unavailable | 1/1 Transceiver Half CANbus 8-SO |  |  |  | NXP USA |  |  | TJA1050 | SOIC-8 NXP USA |  | None
1 |  | USB_C | USB_C_CUSB31-CFM2AX-01-X | no need to buy | USB_C | USB Type-C USB 2.0 Connector
1 | AP2112-3.3 | VREG_SOT23-5 | SOT23-5 | https://www.digikey.com/product-detail/en/diodes-incorporated/AP2112K-3-3TRG1/AP2112K-3-3TRG1DICT-ND/4505257 | U2 | SOT23-5 Fixed Voltage Regulators
1 | WS2812B3535 | WS2812B3535 | LED3535 | https://www.adafruit.com/product/2686 | NEO
1 | XT30PW-M | XT30PW-M | XT30PWM | kevin got it | 24V | 30A Low Temperature Rise Fire Retardant Plug |  | 30A Low Temperature Rise Fire Retardant Plug | 5mm | Amass | XT30PW-M
1 | 32.768 | XTAL-3.2X1.5 | XTAL3215 | https://www.digikey.com/product-detail/en/abracon-llc/ABMM2-32-768MHZ-E2F-T/535-9643-1-ND/1237110 | X4 | Low cost SMT crystals, no capacitors included
a | https://www.digikey.com/product-detail/en/winbond-electronics/W25Q16JVSSIQ/W25Q16JVSSIQ-ND/6193769
 | https://www.digikey.com/product-detail/en/winbond-electronics/W25Q16JVSNIQ/W25Q16JVSNIQ-ND/6193768
b | https://www.digikey.com/product-detail/en/vishay-semiconductor-diodes-division/SSC54-E3-57T/SSC54-E3-57TGICT-ND/1091694

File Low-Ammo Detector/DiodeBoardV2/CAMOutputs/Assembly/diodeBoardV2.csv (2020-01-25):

Qty | Value | Device | Package | Parts | Description
1 | 2PIN | 2PIN | 2PIN | U$2
1 | PLPVQ940A | PLPVQ940A | PLPVQ940A | U$1

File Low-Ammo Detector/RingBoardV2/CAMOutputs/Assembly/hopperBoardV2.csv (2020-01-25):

Qty | Value | Device | Package | Parts | Description | POPULARITY | SPICEPREFIX
1 | 10uF | C-USC0603 | C0603 | C3 | CAPACITOR, American symbol | 37 | C
1 | 180k | R-US_R0603 | R0603 | R2 | RESISTOR, American symbol | 77 | R
1 | 2.2uH | 74479776222 | 74479776222 | U$9
1 | 22pF | C-USC0603 | C0603 | C2 | CAPACITOR, American symbol | 37 | C
2 | 2PIN | 2PIN | 2PIN | U$1, U$2
1 | 330k | R-US_R0603 | R0603 | R1 | RESISTOR, American symbol | 77 | R
1 | 4.7uF | C-USC0603 | C0603 | C1 | CAPACITOR, American symbol | 37 | C
2 | OPL550 | OPL550 | OPL550 | U$3, U$4
1 | SM02B-GHS-TB | SM02B-GHS-TB | SM02B-GHS-TB | U$6
1 | SM03B-GHS-TB | SM03B-GHS-TB | SM03B-GHS-TB | U$8
1 | TPS62260 | TPS62260 | TPS62260 | U$5

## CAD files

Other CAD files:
Robomaster-Controller-Board-v4.0/RMCB4.f3d

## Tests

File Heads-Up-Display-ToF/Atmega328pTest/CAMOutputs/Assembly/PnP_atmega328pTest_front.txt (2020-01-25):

C1	64.67	58.83	90.00	100nF	C0603
C2	68.58	53.34	0.00	1uF	C0603
C3	71.12	81.28	270.00	4.7uF 16V	C1206
C4	68.58	59.05	0.00	1uF	C0603
C5	64.82	74.52	0.00	100nF	C0603
C7	64.14	81.92	270.00	100nF	C0603
C8	69.55	56.16	0.00	4.7uF 16V	C1206
D1	64.77	50.16	270.00	Yellow	LED-0603
D2	43.82	76.50	0.00	Yellow	LED-0603
D3	43.84	79.43	0.00	Yellow	LED-0603
D4	51.97	49.53	270.00	Yellow	LED-0603
IC1	56.52	78.11	90.00	FT232RL	SSOP28-LD
P1	56.64	88.58	180.00	0475890001	MOLEX_0475890001
R1	55.88	67.95	90.00	1K	R0603
R2	53.54	67.95	270.00	1K	R0603
R3	51.36	67.97	270.00	1K	R0603
R4	64.77	54.61	90.00	1K	R0603
R5	48.64	76.50	0.00	1K	R0603
R6	48.74	79.43	0.00	1K	R0603
R7	68.58	66.67	270.00	10K	R0603
R8	68.58	71.76	90.00	10K	R0603
U$1	45.56	56.14	90.00	CSTNE16M0VH3C000R0	CSTNE16M0VH3C000R0
U$2	61.91	67.09	180.00	KSR223GLFG	KSR223GLFG
U$3	67.31	81.80	90.00	SS1P3L-M3/84A	SS1P3L-M3/84A
U1	53.98	58.42	0.00	ATMEGA328P_TQFP	TQFP32-08

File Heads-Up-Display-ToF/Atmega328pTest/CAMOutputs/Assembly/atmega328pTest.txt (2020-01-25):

Partlist exported from C:/Users/Henry/Files/Robomaster/GitHub/Electrical-System/Heads-Up-Display-ToF/Atmega328pTest/atmega328pTest.sch at 1/13/2020 5:40 PM

Qty Value              Device             Package            Parts                  Description                                                                 DESCRIPTION                                                                 DIGI-KEY_PART_NUMBER DIGI-KEY_PURCHASE_URL                                                                                                                                                                      MF                                                                                                                                           MP      MPN        OC_FARNELL OC_NEWARK PACKAGE              POPULARITY PROD_ID  SPICEPREFIX VALUE          
1                      PINHD-1X6          1X06               JP1                    PIN HEADER                                                                                                                                                                                                                                                                                                                                                                                                                                                                                                                                                                                                                       
1   0475890001         0475890001         MOLEX_0475890001   P1                     Conn Micro USB Type AB RCP 5 POS 0.65mm Solder RA SMD 5 Terminal 1 Port T/R   USB - micro AB Receptacle Connector 5 Position Surface Mount, Right Angle  Through Hole        WM17143CT-ND                                                                                                                                                                               https://www.digikey.com/product-detail/en/molex/0475890001/WM17143CT-ND/1832255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 Molex   0475890001                                           None                                           
3   100nF              C-USC0603          C0603              C1, C5, C7             CAPACITOR, American symbol                                                                                                                                                                                                                                                                                                                                                                                                                                                                                                                                                        37                  C                          
2   10K                R-US_R0603         R0603              R7, R8                 RESISTOR, American symbol                                                                                                                                                                                                                                                                                                                                                                                                                                                                                                                                                         77                  R                          
6   1K                 R-US_R0603         R0603              R1, R2, R3, R4, R5, R6 RESISTOR, American symbol                                                                                                                                                                                                                                                                                                                                                                                                                                                                                                                                                         77                  R                          
2   1uF                C-USC0603          C0603              C2, C4                 CAPACITOR, American symbol                                                                                                                                                                                                                                                                                                                                                                                                                                                                                                                                                        37                  C                          
2   4.7uF 16V          C-USC1206          C1206              C3, C8                 CAPACITOR, American symbol                                                                                                                                                                                                                                                                                                                                                                                                                                                                                                                                                        24                  C                          
1   ATMEGA328P_TQFP    ATMEGA328P_TQFP    TQFP32-08          U1                     Popular 328P in QFP                                                                                                                                                                                                                                                                                                                                                                                                                                                                                                                                                                          IC-09069             ATMEGA328P_TQFP
1   CSTNE16M0VH3C000R0 CSTNE16M0VH3C000R0 CSTNE16M0VH3C000R0 U$1                                                                                                                                                                                                                                                                                                                                                                                                                                                                                                                                                                                                                                                     
1   FT232RL            FT232RL            SSOP28-LD          IC1                                                                                                 USB Bridge, USB to UART USB 2.0 UART Interface 28-SSOP                     768-1007-1-ND        https://www.digikey.com/product-detail/en/ftdi-future-technology-devices-international-ltd/FT232RL-REEL/768-1007-1-ND/1836402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 FTDI, Future                                                                                                                                 FT232RL                                 SSOP-28 FTDI, Future                                                
1   ISO                MA03-2             MA03-2             SV1                    PIN HEADER                                                                                                                                                                                                                                                                                                                                                                                                                                                                                                                              unknown    unknown                        15                                             
1   KSR223GLFG         KSR223GLFG         KSR223GLFG         U$2                                                                                                                                                                                                                                                                                                                                                                                                                                                                                                                                                                                                                                                     
1   SS1P3L-M3/84A      SS1P3L-M3/84A      SS1P3L-M3/84A      U$3                                                                                                                                                                                                                                                                                                                                                                                                                                                                                                                                                                                                                                                     
4   Yellow             LED0603            LED-0603           D1, D2, D3, D4         LED (Generic)

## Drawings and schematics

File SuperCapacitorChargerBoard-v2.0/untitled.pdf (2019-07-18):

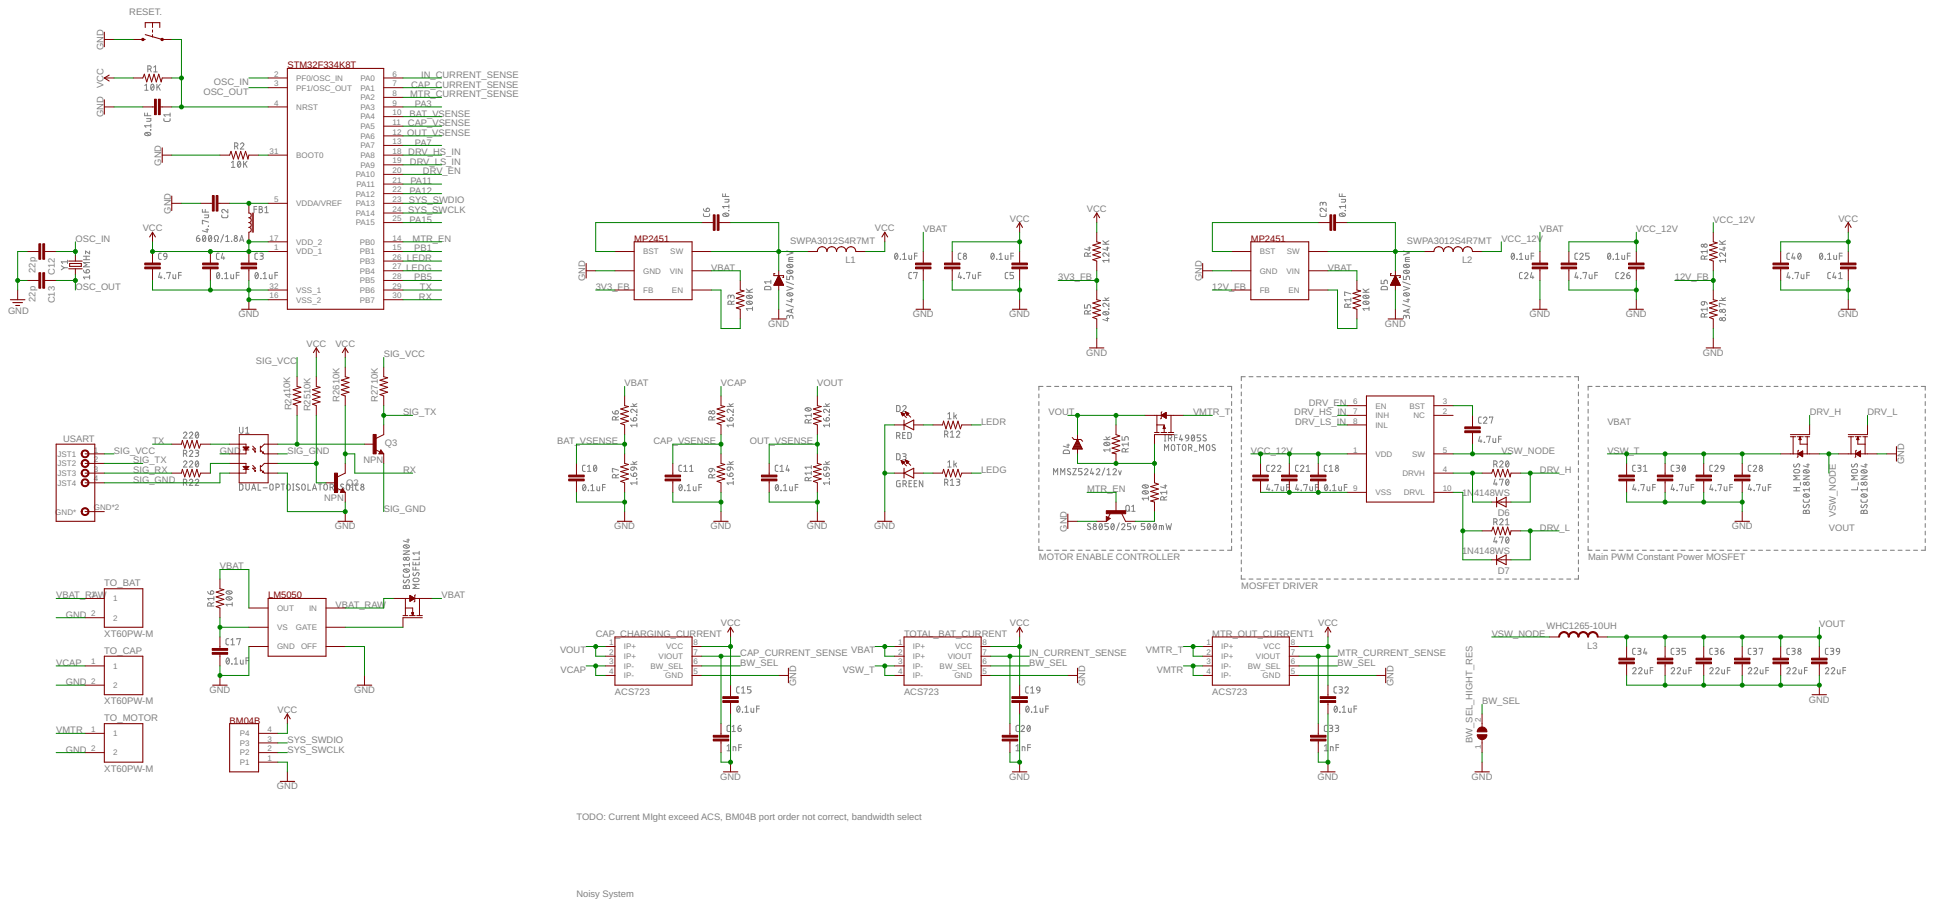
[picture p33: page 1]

GND GND

Main PWM Constant Power MOSFET MOSFET DRIVER MOTOR ENABLE CONTROLLER

TODO: Current MIght exceed ACS, BM04B port order not correct, bandwidth select

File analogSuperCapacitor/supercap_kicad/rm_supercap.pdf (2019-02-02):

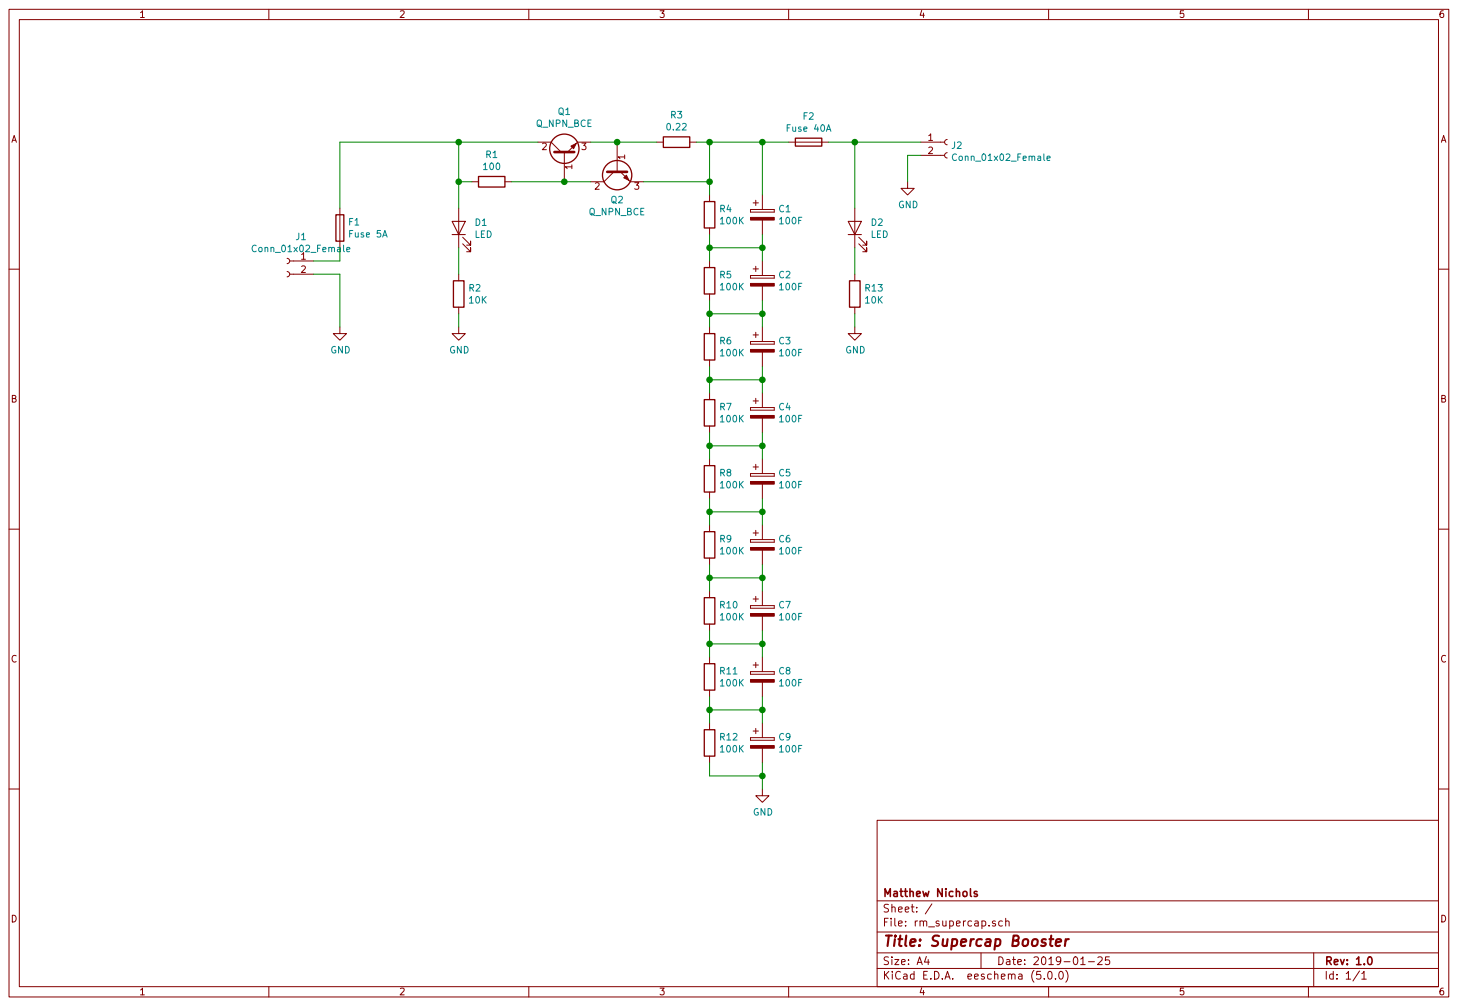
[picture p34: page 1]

File: rm_supercap.sch Sheet: / Matthew Nichols

Id: 1/1 Title: Supercap Booster

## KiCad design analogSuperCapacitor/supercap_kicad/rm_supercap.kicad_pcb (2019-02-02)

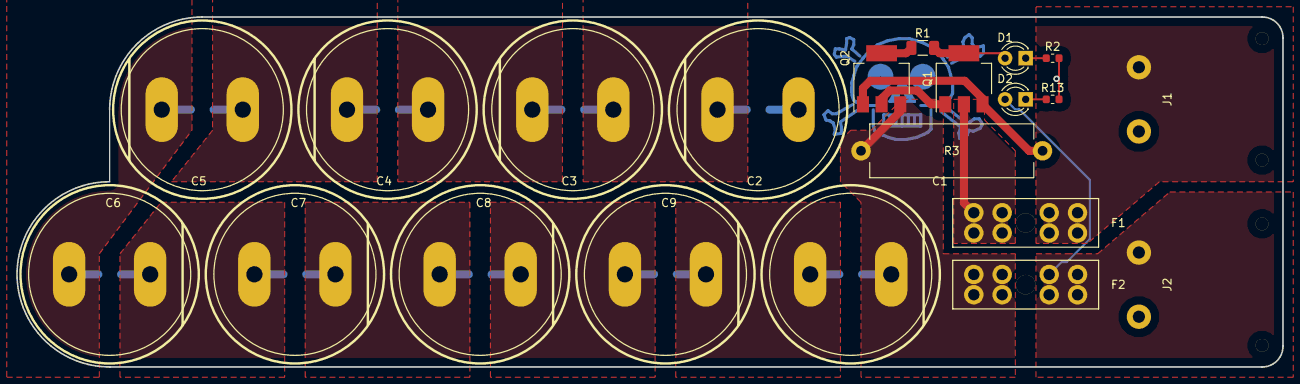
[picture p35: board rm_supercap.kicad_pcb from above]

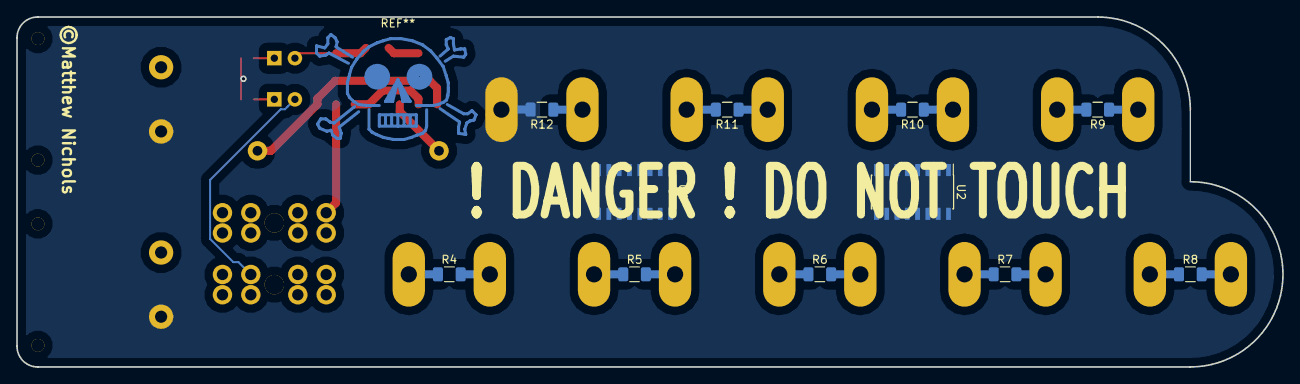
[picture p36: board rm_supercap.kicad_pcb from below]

Board: 2 copper layers, 156.2 x 43.2 mm, 32 parts (11 on the bottom side), 17 nets.

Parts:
C1, C2, C3, C4, C5, C6, C7, C8, C9: 100F; CAP_10mm
D1, D2: LED; LED_D3.0mm
F1: Fuse 5A; fuse_holder
F2: Fuse 40A; fuse_holder
J1, J2: Conn_01x02_Female; H10710
Q1, Q2: Q_NPN_BCE; SOT-223-3_TabPin2
R1: 100; R_1206_3216Metric
R2, R13: 10K; R_0603_1608Metric
R3: 0.22; R_Axial_Power_L20.0mm_W6.4mm_P22.40mm
R4, R5, R6, R7, R8, R9, R10, R11, R12: 100K; R_1206_3216Metric
U1, U2: ALD810027; SOIC-16_3.9x9.9mm_P1.27mm

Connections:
GND: C9.2, J1.2, J2.2, R2.2, R12.2, R13.2
unnamed: C1.1, F2.2, Q2.3, R3.1, R4.1, U1.11
unnamed: C1.2, C2.1, R4.2, R5.1, U1.6, U1.7, U1.9
unnamed: C2.2, C3.1, R5.2, R6.1, U1.8
unnamed: C3.2, C4.1, R6.2, R7.1, U2.2, U2.3
unnamed: C4.2, C5.1, R7.2, R8.1, U2.4, U2.14, U2.15
unnamed: C5.2, C6.1, R8.2, R9.1, U2.11
unnamed: C6.2, C7.1, R9.2, R10.1, U2.6, U2.7, U2.9
unnamed: C7.2, C8.1, R10.2, R11.1, U2.8
unnamed: C8.2, C9.1, R11.2, R12.1
unnamed: D1.1, R2.1
unnamed: D1.2, F1.1, Q1.2, R1.2
unnamed: D2.1, R13.1
unnamed: D2.2, F2.1, J2.1
unnamed: F1.2, J1.1
unnamed: Q1.1, Q2.2, R1.1
unnamed: Q1.3, Q2.1, R3.2

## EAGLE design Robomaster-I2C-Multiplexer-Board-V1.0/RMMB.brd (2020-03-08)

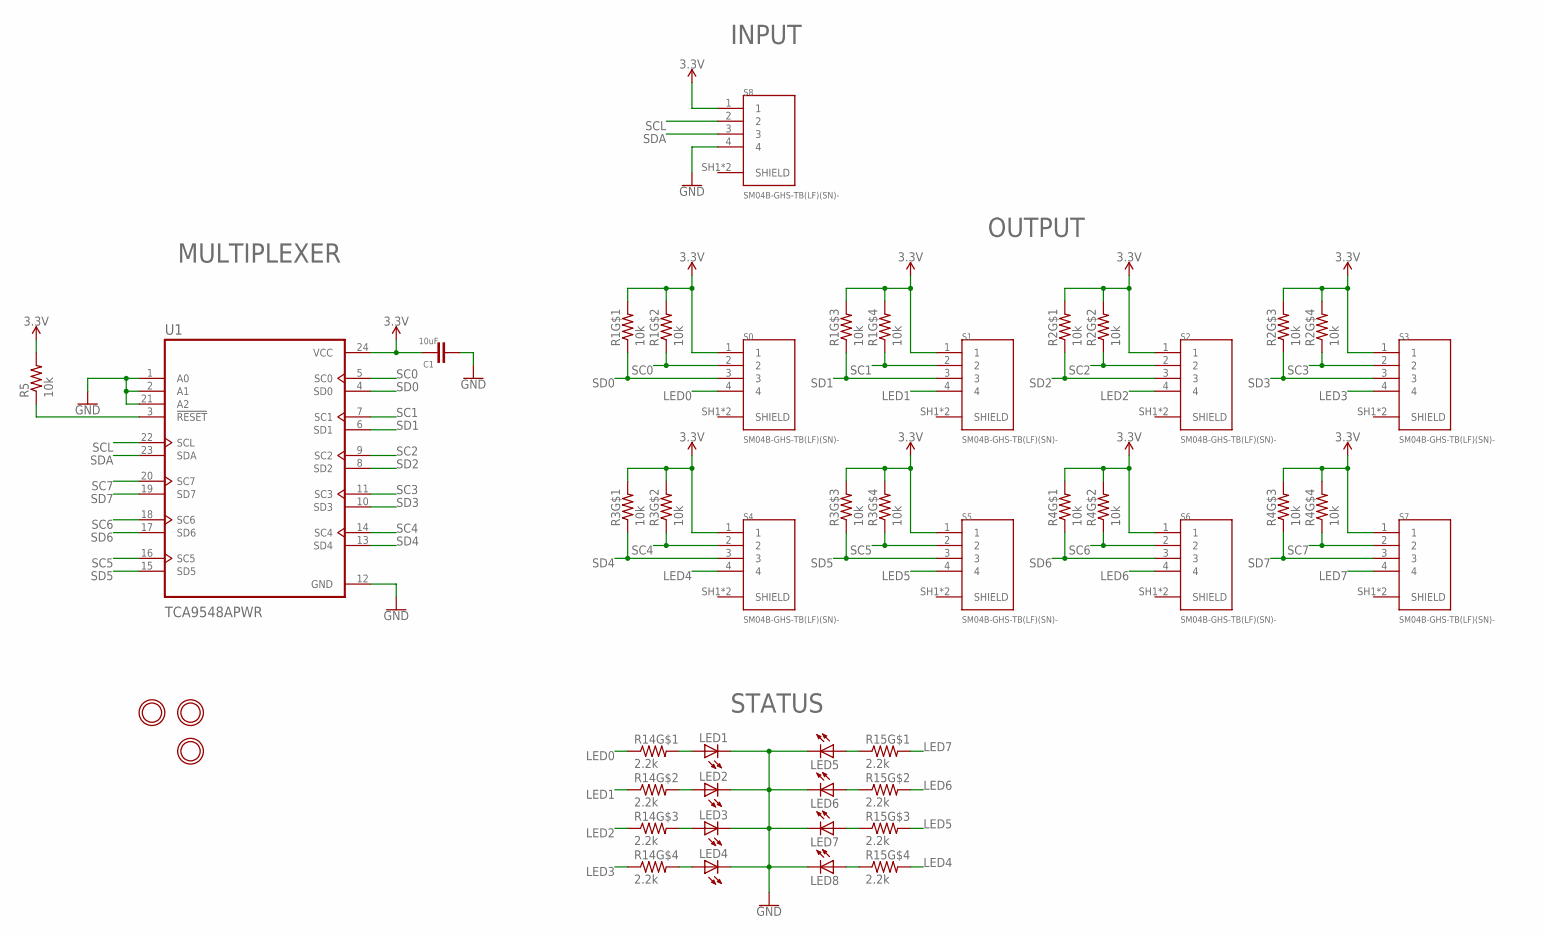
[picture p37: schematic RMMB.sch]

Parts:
C1: 10uF; C0603
LED1, LED2, LED3, LED4, LED5, LED6, LED7, LED8: LEDCHIP-LED0603; CHIP-LED0603
R1, R2, R3, R4: 10k; RESPACK_4X0603
R5: 10k; R0603
R14, R15: 2.2k; RESPACK_4X0603
S0, S1, S2, S3, S4, S5, S6, S7, S8: SM04B-GHS-TB(LF)(SN)-; JST_SM04B-GHS-TB(LF)(SN)-
U1: TCA9548APWR; SOP65P640X120-24N
U$1, U$2, U$31: MOUNTINGHOLE2.5; MOUNTINGHOLE_2.5_PLATED

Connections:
3.3V: C1.1, R1.5 (2), R1.6 (2), R1.7 (2), R1.8 (2), R2.5 (2), R2.6 (2), R2.7 (2), R2.8 (2), R3.5 (2), R3.6 (2), R3.7 (2), R3.8 (2), R4.5 (2), R4.6 (2), R4.7 (2), R4.8 (2), R5.2, S0.1, S1.1, S2.1, S3.1, S4.1, S5.1, S6.1, S7.1, S8.1, U1.24 (VCC)
GND: C1.2, LED1.C, LED2.C, LED3.C, LED4.C, LED5.C, LED6.C, LED7.C, LED8.C, S8.4, U1.1 (A0), U1.2 (A1), U1.12 (GND), U1.21 (A2)
LED0: R14.1, S0.4
LED1: R14.2 (1), S1.4
LED2: R14.3 (1), S2.4
LED3: R14.4 (1), S3.4
LED4: R15.5 (2), S4.4
LED5: R15.6 (2), S5.4
LED6: R15.7 (2), S6.4
LED7: R15.8 (2), S7.4
unnamed: LED1.A, R14.8 (2)
unnamed: R5.1, U1.3 (!RESET)
unnamed: LED2.A, R14.7 (2)
unnamed: LED3.A, R14.6 (2)
unnamed: LED4.A, R14.5 (2)
unnamed: LED5.A, R15.1
unnamed: LED6.A, R15.2 (1)
unnamed: LED7.A, R15.3 (1)
unnamed: LED8.A, R15.4 (1)
SC0: R1.2 (1), S0.2, U1.5 (SC0)
SC1: R1.4 (1), S1.2, U1.7 (SC1)
SC2: R2.2 (1), S2.2, U1.9 (SC2)
SC3: R2.4 (1), S3.2, U1.11 (SC3)
SC4: R3.2 (1), S4.2, U1.14 (SC4)
SC5: R3.4 (1), S5.2, U1.16 (SC5)
SC6: R4.2 (1), S6.2, U1.18 (SC6)
SC7: R4.4 (1), S7.2, U1.20 (SC7)
SCL: S8.2, U1.22 (SCL)
SD0: R1.1, S0.3, U1.4 (SD0)
SD1: R1.3 (1), S1.3, U1.6 (SD1)
SD2: R2.1, S2.3, U1.8 (SD2)
SD3: R2.3 (1), S3.3, U1.10 (SD3)
SD4: R3.1, S4.3, U1.13 (SD4)
SD5: R3.3 (1), S5.3, U1.15 (SD5)
SD6: R4.1, S6.3, U1.17 (SD6)
SD7: R4.3 (1), S7.3, U1.19 (SD7)
SDA: S8.3, U1.23 (SDA)
SHIELD: S0.SH1 (SHIELD), S0.SH2 (SHIELD), S1.SH1 (SHIELD), S1.SH2 (SHIELD), S2.SH1 (SHIELD), S2.SH2 (SHIELD), S3.SH1 (SHIELD), S3.SH2 (SHIELD), S4.SH1 (SHIELD), S4.SH2 (SHIELD), S5.SH1 (SHIELD), S5.SH2 (SHIELD), S6.SH1 (SHIELD), S6.SH2 (SHIELD), S7.SH1 (SHIELD), S7.SH2 (SHIELD), S8.SH1 (SHIELD), S8.SH2 (SHIELD)

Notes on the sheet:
INPUT
OUTPUT
STATUS
MULTIPLEXER

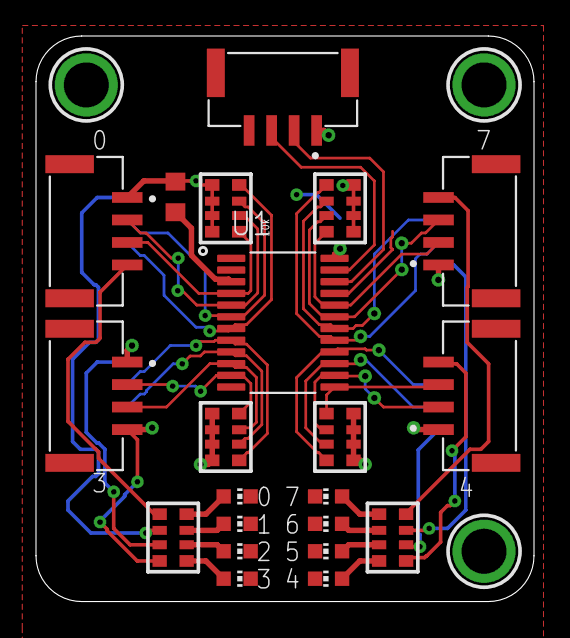
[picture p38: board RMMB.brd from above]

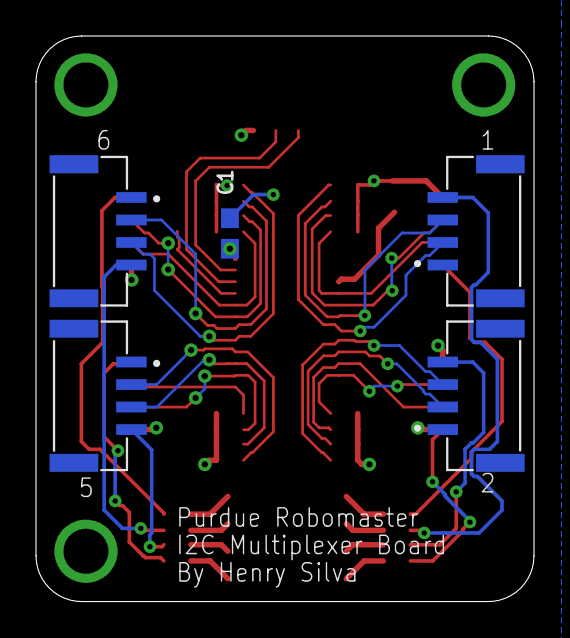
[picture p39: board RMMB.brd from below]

Board: 2 copper layers, 27.7 x 31.4 mm, 29 parts (5 on the bottom side), 38 nets.

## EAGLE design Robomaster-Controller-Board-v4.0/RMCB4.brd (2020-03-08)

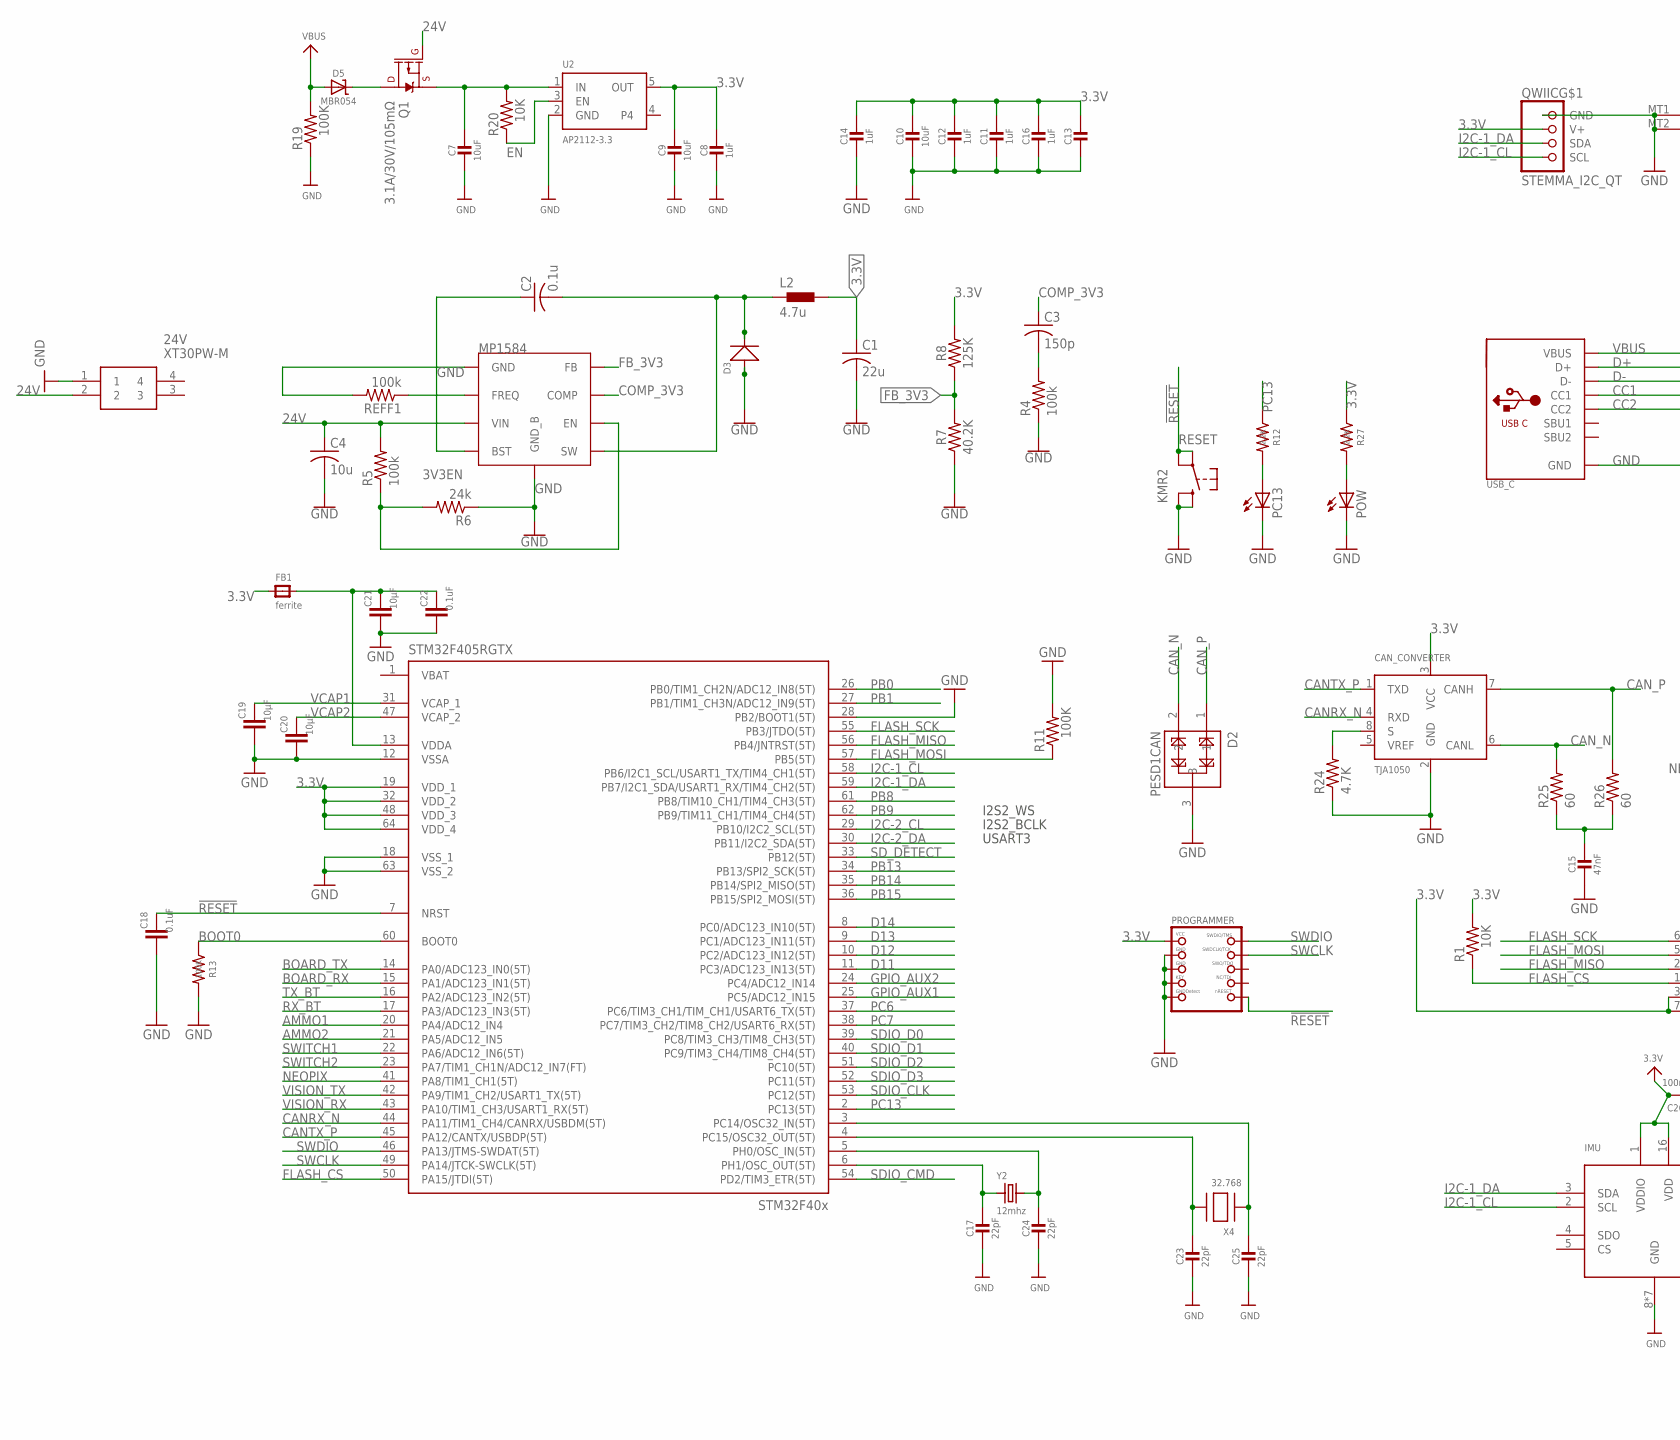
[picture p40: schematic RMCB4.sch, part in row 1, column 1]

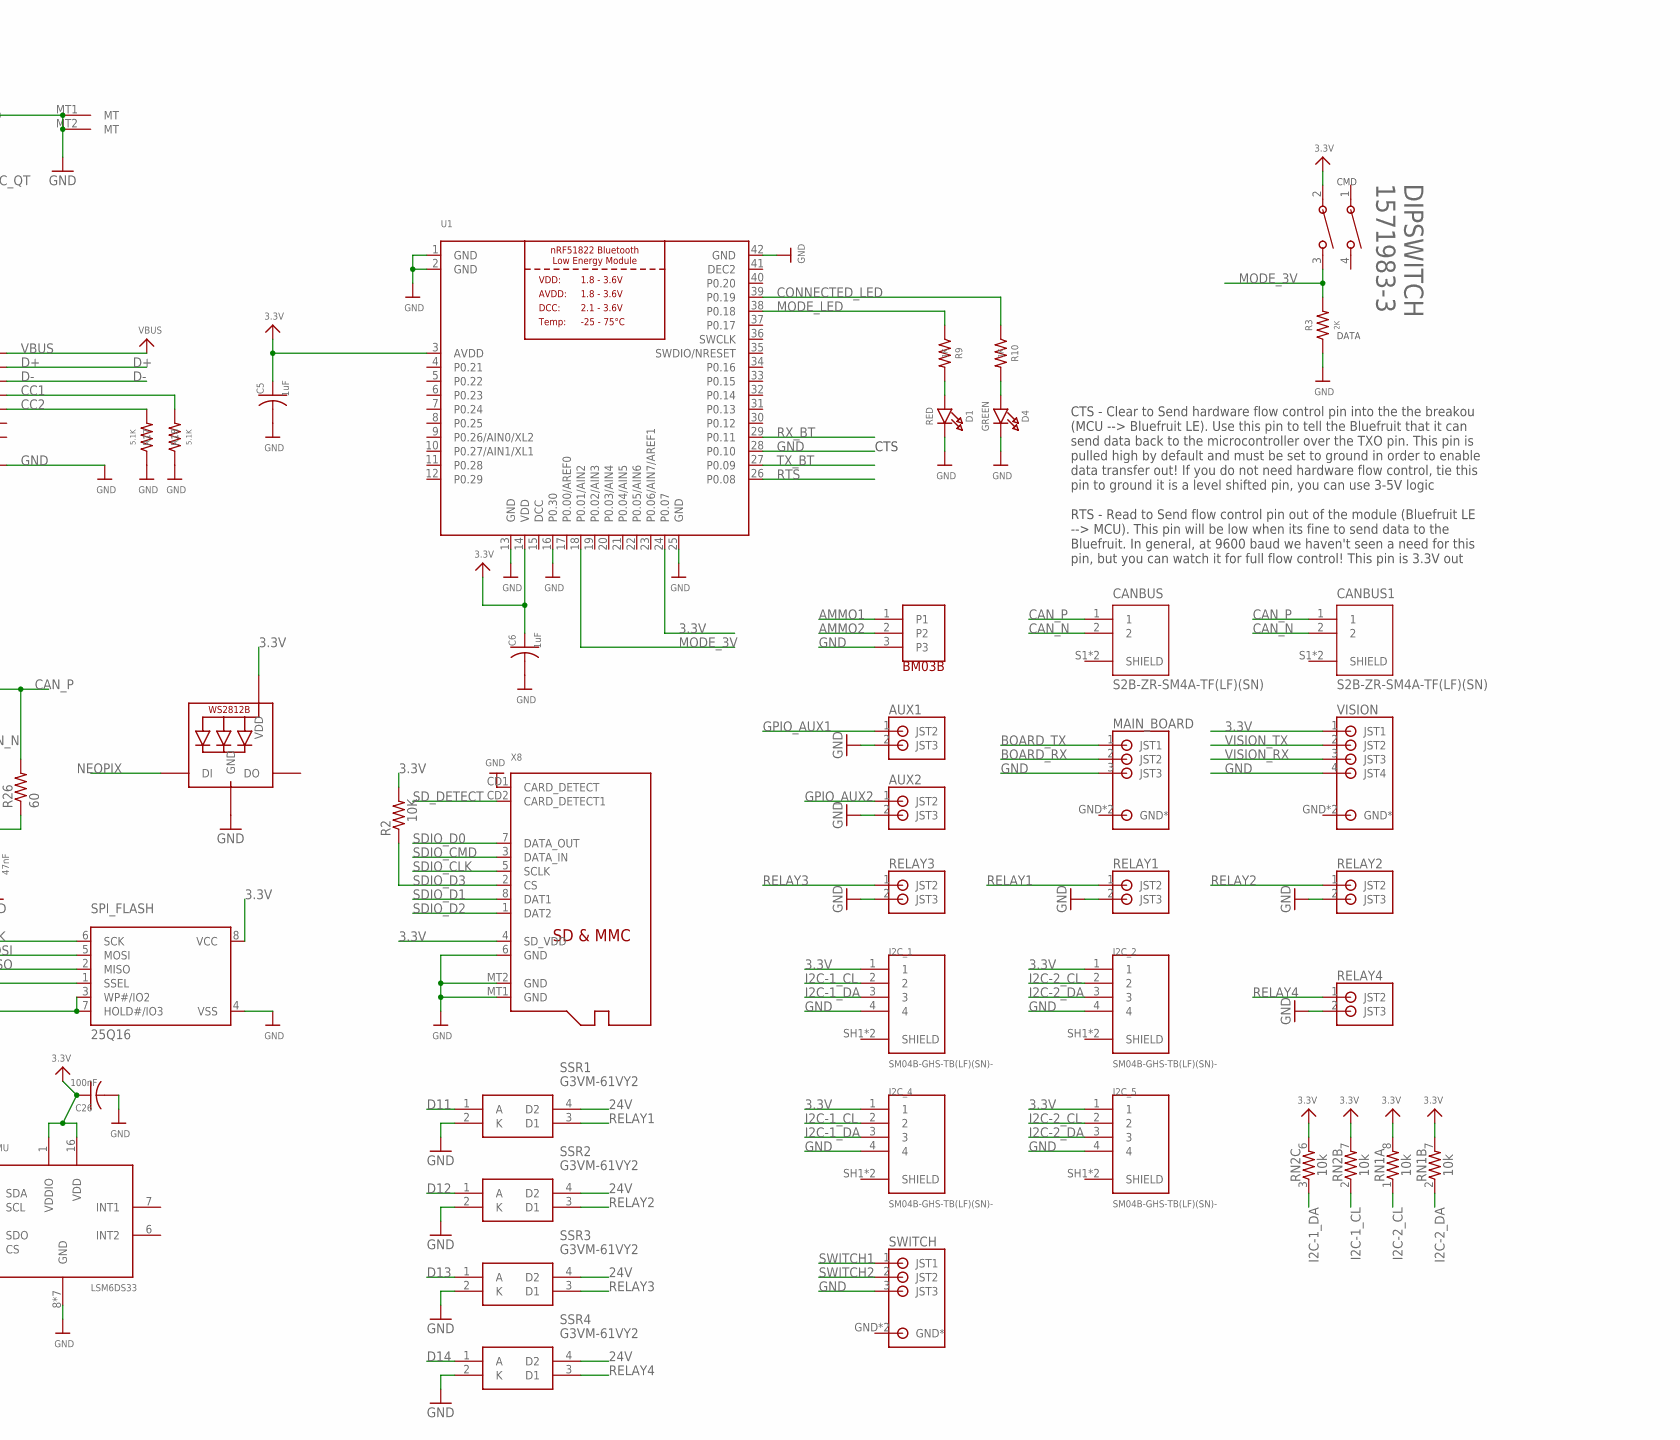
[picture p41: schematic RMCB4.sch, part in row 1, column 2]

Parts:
24V: XT30PW-M; XT30PWM
AMMO_DETEC: BM03-GHS_TBT; BM03-GHS-TBT
AUX1, AUX2: S2B-PH-SM4_TB
C1: 22u; C1206
C2: 0.1u; C0603
C3: 150p; C0603
C4: 10u; C1206
C5, C6: 1uF; C0603
C7, C9, C10: 10uF; 0603-NO
C8, C11, C12, C13, C14, C16: 1uF; 0603-NO
C15: 47nF; 0603-NO
C17, C23, C24, C25: 22pF; 0603-NO
C18, C22: 0.1uF; C0603
C19, C20, C21: 10µF; C0603
C26: 100nF; C0603
CANBUS, CANBUS1: S2B-ZR-SM4A-TF(LF)(SN); JST_S2B-ZR-SM4A-TF(LF)(SN)
CAN_CONVERTER: TJA1050; SOT96-1
D1: RED; CHIPLED_0805_NOOUTLINE
D2: PESD1CAN; SOT23-3
D3: SMD-DIODE-SCHOTTKY-40V-3A(DO-214AB); DO-214AB
D4: GREEN; CHIPLED_0805_NOOUTLINE
D5: MBR054; SOD-123
DIPSWITCH: 1571983-3; SWSO4_300X100P50B
FB1: ferrite; 0805-NO@1
I2C_1, I2C_2, I2C_4, I2C_5: SM04B-GHS-TB(LF)(SN)-; JST_SM04B-GHS-TB(LF)(SN)-
IMU: LSM6DS33; LGA16_3X3MM
L2: 4.7u; MHCI0603-4R7M-R8
MAIN_BOARD: S3B-PH-SM4_TB
NEO: WS2812B3535; LED3535
PC13: LEDCHIPLED_0603; CHIPLED_0603
POW: LEDCHIPLED_0603; CHIPLED_0603
PROGRAMMER: JTAG-CORTEX; 2X05_1.27MM_SMT
Q1: 3.1A/30V/105mΩ; SOT23-3
QWIIC: STEMMA_I2C_QT; JST_SH4
R1, R2, R20: 10K; R0603
R3: 2K; R0603
R4, R5: 100k; R0603
R6: 24k; R0603
R7: 40.2K; 0603
R8: 125K; 0603
R9, R10: 1K; R0603
R11, R13, R19: 100K; R0603
R12, R27: 2.2K; R0603
R17, R18: 5.1K; R0603
R24: 4.7K; R0603
R25, R26: 60; R0603
REFF1: 100k; R0603
RELAY1, RELAY2, RELAY3, RELAY4: S2B-PH-SM4_TB
RESET: KMR2; BTN_KMR2_4.6X2.8
RN1, RN2: 10k; 0805-ARV
SPI_FLASH: 25Q16; SOIC8_150MIL
SSR1, SSR2, SSR3, SSR4: G3VM-61VY2; SOP254P700X230-4N
STM32F405RGTX: STM32F405R; TQFP64
SWITCH: S3B-PH-SM4_TB
U1: NRF51822_MODULE_MDBT40; BLE_MODULE_RAYTAC_MDBT40
U2: AP2112-3.3; SOT23-5
U$10: MP1584_V2
USB_C: USB_C; USB_C_CUSB31-CFM2AX-01-X
VISION: S4B-PH-SM4_TB
X4: 32.768; XTAL3215
X8: MICROSD
Y2: 12mhz; CRYSTAL_2.5X2

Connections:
3.3V: C1.1, C5.1, C6.1, C8.1, C9.1, C10.1, C11.1, C12.1, C13.1, C14.1, C16.1, C26.1, CAN_CONVERTER.3 (VCC), DIPSWITCH.2, FB1.1, I2C_1.1, I2C_2.1, I2C_4.1, I2C_5.1, IMU.1 (VDDIO), IMU.16 (VDD), L2.P$2 (2), NEO.2 (VDD), PROGRAMMER.1 (VCC), QWIIC.2 (V+), R1.2, R2.2, R8.2, R27.1, RN1.7 (2), RN1.8 (2), RN2.6 (2), RN2.7 (2), SPI_FLASH.3 (WP#/IO2), SPI_FLASH.7 (HOLD#/IO3), SPI_FLASH.8 (VCC), STM32F405RGTX.19 (VDD_1), STM32F405RGTX.32 (VDD_2), STM32F405RGTX.48 (VDD_3), STM32F405RGTX.64 (VDD_4), U1.3 (AVDD), U1.14 (VDD), U1.24 (P0.07), U2.5 (OUT), VISION.1 (JST1), X8.4 (SD_VDD)
3V3EN: R5.1, R6.2, U$10.EN
24V: 24V.2, C4.1, Q1.1 (G), R5.2, SSR1.4 (D2), SSR2.4 (D2), SSR3.4 (D2), SSR4.4 (D2), U$10.VIN
!RESET: C18.1, PROGRAMMER.10 (NRESET), RESET.A, RESET.A' (P1), STM32F405RGTX.7 (NRST)
AMMO1: AMMO_DETEC.1, STM32F405RGTX.20 (PA4/ADC12_IN4)
AMMO2: AMMO_DETEC.2, STM32F405RGTX.21 (PA5/ADC12_IN5)
BOARD_RX: MAIN_BOARD.2 (JST2), STM32F405RGTX.15 (PA1/ADC123_IN1(5T))
BOARD_TX: MAIN_BOARD.1 (JST1), STM32F405RGTX.14 (PA0/ADC123_IN0(5T))
BOOT0: R13.1, STM32F405RGTX.60 (BOOT0)
BST1: C2.1, U$10.BST
CANRX_N: CAN_CONVERTER.4 (RXD), STM32F405RGTX.44 (PA11/TIM1_CH4/CANRX/USBDM(5T))
CANTX_P: CAN_CONVERTER.1 (TXD), STM32F405RGTX.45 (PA12/CANTX/USBDP(5T))
CAN_N: CANBUS.2, CANBUS1.2, CAN_CONVERTER.6 (CANL), D2.2, R25.2
CAN_P: CANBUS.1, CANBUS1.1, CAN_CONVERTER.7 (CANH), D2.1, R26.2
CC1: R18.2, USB_C.A5 (CC1)
CC2: R17.2, USB_C.B5 (CC2)
COMP_3V3: C3.1, U$10.COMP
CONNECTED_LED: R10.1, U1.39 (P0.19)
D11: SSR1.1 (A), STM32F405RGTX.11 (PC3/ADC123_IN13(5T))
D12: SSR2.1 (A), STM32F405RGTX.10 (PC2/ADC123_IN12(5T))
D13: SSR3.1 (A), STM32F405RGTX.9 (PC1/ADC123_IN11(5T))
D14: SSR4.1 (A), STM32F405RGTX.8 (PC0/ADC123_IN10(5T))
D+: USB_C.A6 (D+), USB_C.B6 (D+)
D-: USB_C.A7 (D-), USB_C.B7 (D-)
DCC: U1.15 (DCC)
DEC2: U1.41 (DEC2)
EN: R20.1, U2.3 (EN)
FB_3V3: R7.2, R8.1, U$10.FB
FLASH_CS: R1.1, SPI_FLASH.1 (SSEL), STM32F405RGTX.50 (PA15/JTDI(5T))
FLASH_MISO: SPI_FLASH.2 (MISO), STM32F405RGTX.56 (PB4/JNTRST(5T))
FLASH_MOSI: R11.1, SPI_FLASH.5 (MOSI), STM32F405RGTX.57 (PB5(5T))
FLASH_SCK: SPI_FLASH.6 (SCK), STM32F405RGTX.55 (PB3/JTDO(5T))
FREQ1: REFF1.1, U$10.FREQ
GND: 24V.1, AMMO_DETEC.3, AUX1.2 (JST3), AUX2.2 (JST3), C1.2, C4.2, C5.2, C6.2, C7.2, C8.2, C9.2, C10.2, C11.2, C12.2, C13.2, C14.2, C15.2, C16.2, C17.2, C18.2, C19.2, C20.2, C21.2, C22.2, C23.2, C24.2, C25.2, C26.2, CAN_CONVERTER.2 (GND), D1.C, D2.3, D3.1 (+), D4.C, I2C_1.4, I2C_2.4, I2C_4.4, I2C_5.4, IMU.8 (GND), IMU.9 (GND), IMU.10 (GND), IMU.11 (GND), IMU.12 (GND), IMU.13 (GND), IMU.15 (GND), MAIN_BOARD.3 (JST3), NEO.4 (GND), PC13.C, POW.C, PROGRAMMER.3 (GND), PROGRAMMER.5 (GND), PROGRAMMER.7 (KEY), PROGRAMMER.9 (GNDDETECT), QWIIC.1 (GND), QWIIC.MT1 (MT), QWIIC.MT2 (MT), R3.1, R4.1, R6.1, R7.1, R11.2, R13.2, R17.1, R18.1, R19.1, R24.1, REFF1.2, RELAY1.2 (JST3), RELAY2.2 (JST3), RELAY3.2 (JST3), RELAY4.2 (JST3), RESET.B (S), RESET.B' (S1), SPI_FLASH.4 (VSS), SSR1.2 (K), SSR2.2 (K), SSR3.2 (K), SSR4.2 (K), STM32F405RGTX.12 (VSSA), STM32F405RGTX.18 (VSS_1), STM32F405RGTX.28 (PB2/BOOT1(5T)), STM32F405RGTX.63 (VSS_2), SWITCH.3 (JST3), U1.1 (GND), U1.2 (GND), U1.13 (GND), U1.16 (P0.30), U1.25 (GND), U1.28 (P0.10), U1.42 (GND), U2.2 (GND), U$10.GND, U$10.GND_B, USB_C.A1B12 (GND), USB_C.B1A12 (GND), VISION.4 (JST4), X8.6 (GND), X8.CD1 (CARD_DETECT), X8.MT1 (GND), X8.MT2 (GND)
GPIO_AUX1: AUX1.1 (JST2), STM32F405RGTX.25 (PC5/ADC12_IN15)
GPIO_AUX2: AUX2.1 (JST2), STM32F405RGTX.24 (PC4/ADC12_IN14)
I2C-1_CL: I2C_1.2, I2C_4.2, IMU.2 (SCL), QWIIC.4 (SCL), RN2.2 (1), STM32F405RGTX.58 (PB6/I2C1_SCL/USART1_TX/TIM4_CH1(5T))
I2C-1_DA: I2C_1.3, I2C_4.3, IMU.3 (SDA), QWIIC.3 (SDA), RN2.3 (1), STM32F405RGTX.59 (PB7/I2C1_SDA/USART1_RX/TIM4_CH2(5T))
I2C-2_CL: I2C_2.2, I2C_5.2, RN1.1, STM32F405RGTX.29 (PB10/I2C2_SCL(5T))
I2C-2_DA: I2C_2.3, I2C_5.3, RN1.2 (1), STM32F405RGTX.30 (PB11/I2C2_SDA(5T))
MODE_3V: DIPSWITCH.3, R3.2, U1.18 (P0.01/AIN2)
MODE_LED: R9.1, U1.38 (P0.18)
unnamed: C3.2, R4.2
unnamed: D1.A, R9.2
unnamed: D4.A, R10.2
unnamed: C25.1, STM32F405RGTX.3 (PC14/OSC32_IN(5T)), X4.P$1
unnamed: C23.1, STM32F405RGTX.4 (PC15/OSC32_OUT(5T)), X4.P$2
unnamed: C24.1, STM32F405RGTX.5 (PH0/OSC_IN(5T)), Y2.3 (2)
unnamed: C17.1, STM32F405RGTX.6 (PH1/OSC_OUT(5T)), Y2.1
unnamed: PC13.A, R12.2
unnamed: C21.1, C22.1, FB1.2, STM32F405RGTX.13 (VDDA)
unnamed: CAN_CONVERTER.8 (S), R24.2
unnamed: C15.1, R25.1, R26.1
unnamed: POW.A, R27.2
unnamed: D5.C, Q1.3 (D)
NEOPIX: NEO.1 (DI), STM32F405RGTX.41 (PA8/TIM1_CH1(5T))
PB0: STM32F405RGTX.26 (PB0/TIM1_CH2N/ADC12_IN8(5T))
PB1: STM32F405RGTX.27 (PB1/TIM1_CH3N/ADC12_IN9(5T))
PB8: STM32F405RGTX.61 (PB8/TIM10_CH1/TIM4_CH3(5T))
PB9: STM32F405RGTX.62 (PB9/TIM11_CH1/TIM4_CH4(5T))
PB13: STM32F405RGTX.34 (PB13/SPI2_SCK(5T))
PB14: STM32F405RGTX.35 (PB14/SPI2_MISO(5T))
PB15: STM32F405RGTX.36 (PB15/SPI2_MOSI(5T))
PC6: STM32F405RGTX.37 (PC6/TIM3_CH1/TIM_CH1/USART6_TX(5T))
PC7: STM32F405RGTX.38 (PC7/TIM3_CH2/TIM8_CH2/USART6_RX(5T))
PC13: R12.1, STM32F405RGTX.2 (PC13(5T))
RELAY1: RELAY1.1 (JST2), SSR1.3 (D1)
RELAY2: RELAY2.1 (JST2), SSR2.3 (D1)
RELAY3: RELAY3.1 (JST2), SSR3.3 (D1)
RELAY4: RELAY4.1 (JST2), SSR4.3 (D1)
RTS: U1.26 (P0.08)
RX_BT: STM32F405RGTX.17 (PA3/ADC123_IN3(5T)), U1.29 (P0.11)
SDIO_CLK: STM32F405RGTX.53 (PC12(5T)), X8.5 (SCLK)
SDIO_CMD: STM32F405RGTX.54 (PD2/TIM3_ETR(5T)), X8.3 (DATA_IN)
SDIO_D0: STM32F405RGTX.39 (PC8/TIM3_CH3/TIM8_CH3(5T)), X8.7 (DATA_OUT)
SDIO_D1: STM32F405RGTX.40 (PC9/TIM3_CH4/TIM8_CH4(5T)), X8.8 (DAT1)
SDIO_D2: STM32F405RGTX.51 (PC10(5T)), X8.1 (DAT2)
SDIO_D3: R2.1, STM32F405RGTX.52 (PC11(5T)), X8.2 (CS)
SD_DETECT: STM32F405RGTX.33 (PB12(5T)), X8.CD2 (CARD_DETECT1)
SHIELD: I2C_1.SH1 (SHIELD), I2C_1.SH2 (SHIELD), I2C_2.SH1 (SHIELD), I2C_2.SH2 (SHIELD), I2C_4.SH1 (SHIELD), I2C_4.SH2 (SHIELD), I2C_5.SH1 (SHIELD), I2C_5.SH2 (SHIELD)
SW1: C2.2, D3.2 (-), L2.P$1 (1), U$10.SW
SWCLK: PROGRAMMER.4 (SWDCLK), STM32F405RGTX.49 (PA14/JTCK-SWCLK(5T))
SWDIO: PROGRAMMER.2 (SWDIO), STM32F405RGTX.46 (PA13/JTMS-SWDAT(5T))
SWITCH1: STM32F405RGTX.22 (PA6/ADC12_IN6(5T)), SWITCH.1 (JST1)
SWITCH2: STM32F405RGTX.23 (PA7/TIM1_CH1N/ADC12_IN7(FT)), SWITCH.2 (JST2)
TX_BT: STM32F405RGTX.16 (PA2/ADC123_IN2(5T)), U1.27 (P0.09)
VBUS: D5.A, R19.2, USB_C.A4B9 (VBUS), USB_C.B4A9 (VBUS)
VCAP1: C19.1, STM32F405RGTX.31 (VCAP_1)
VCAP2: C20.1, STM32F405RGTX.47 (VCAP_2)
VHI: C7.1, Q1.2 (S), R20.2, U2.1 (IN)
VISION_RX: STM32F405RGTX.43 (PA10/TIM1_CH3/USART1_RX(5T)), VISION.3 (JST3)
VISION_TX: STM32F405RGTX.42 (PA9/TIM1_CH2/USART1_TX(5T)), VISION.2 (JST2)

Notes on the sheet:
USART3
I2S2_WS
I2S2_BCLK
DATA
CMD
CTS - Clear to Send hardware flow control pin into the the breakou (MCU --> Bluefruit LE). Use this pin to tell the Bluefruit that it can send data back to the microcontroller over the TXO pin. This pin is pulled high by default and must be set to ground in order to enable data transfer out! If you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
CTS

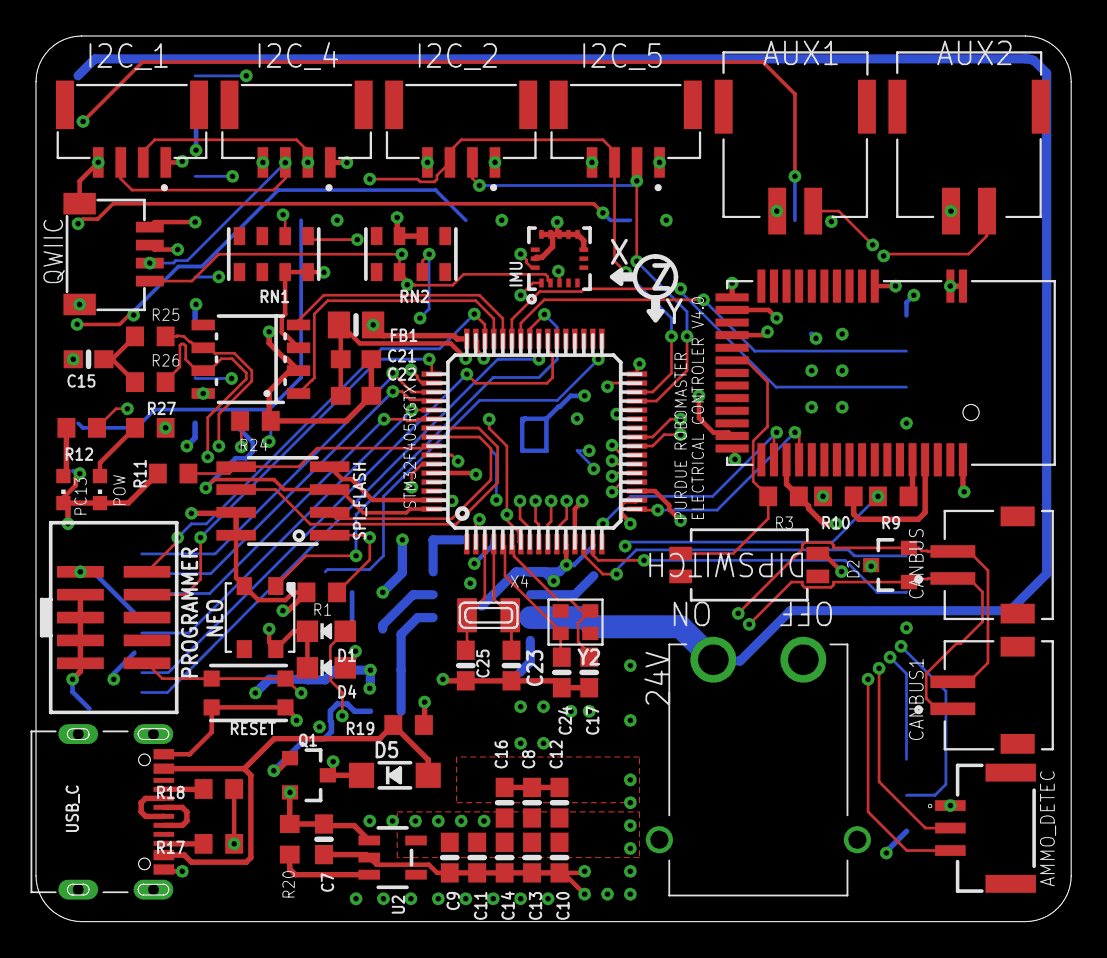
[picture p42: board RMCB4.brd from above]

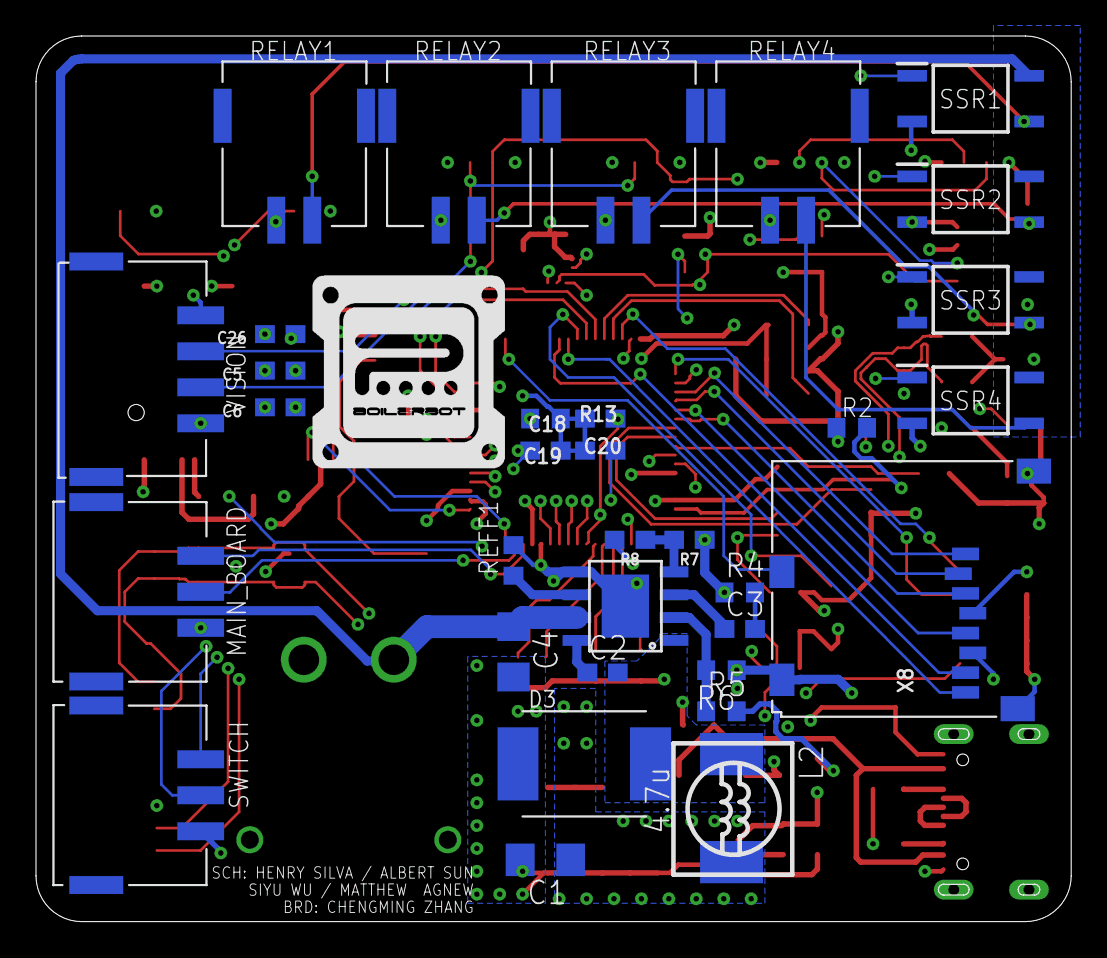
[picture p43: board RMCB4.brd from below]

Board: 4 copper layers, 57.5 x 49.2 mm, 97 parts (33 on the bottom side), 80 nets.

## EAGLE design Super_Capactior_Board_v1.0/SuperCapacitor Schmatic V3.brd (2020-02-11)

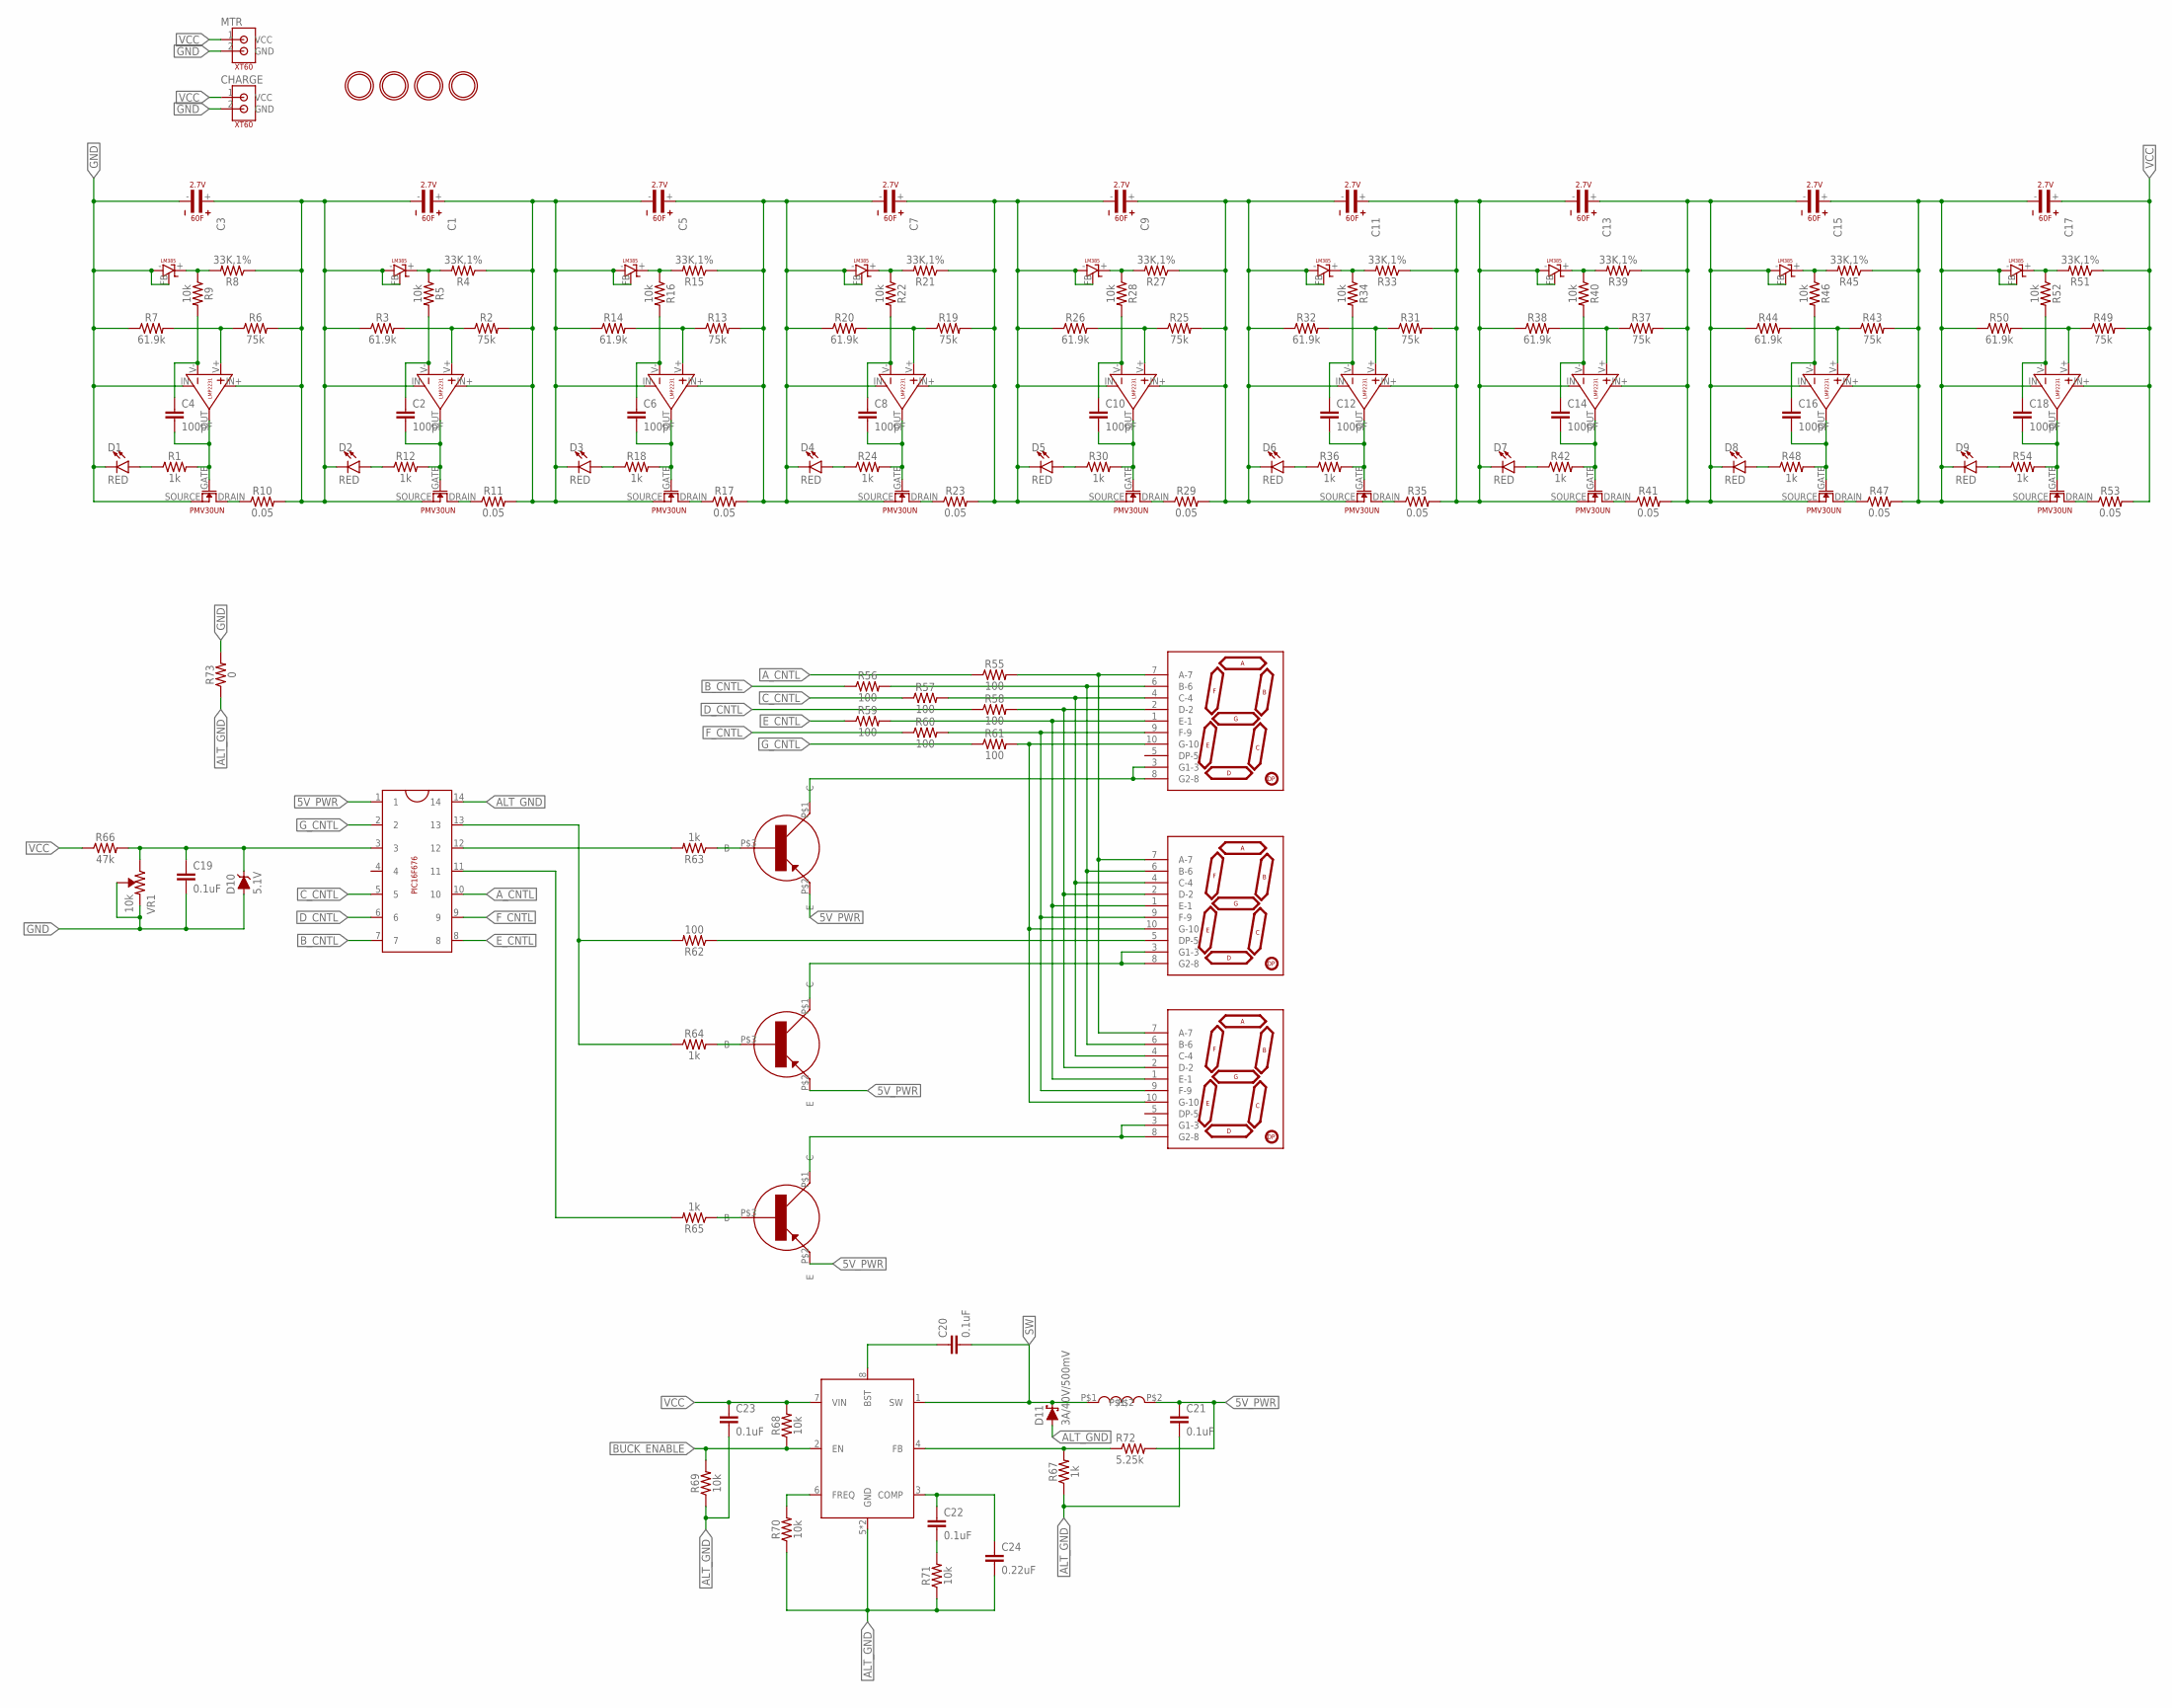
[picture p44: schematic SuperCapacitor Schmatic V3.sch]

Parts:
3.3V_BUCK: SOIC8E; SOIC127P600X170-9N
C1, C3, C5, C7, C9, C11, C13, C15, C17: 2.7V 60F; 2.7V_60F
C2, C4, C6, C8, C10, C12, C14, C16, C18: 100pF; 0603
C19, C20, C21, C22, C23: 0.1uF; 0603
C24: 0.22uF; 0603
CHARGE: XT60_CIRCLE
D1, D2, D3, D4, D5, D6, D7, D8, D9: RED; LED-0603
D10: 5.1V; SOD-323
D11: 3A/40V/500mV; SMA-DIODE
MTR: XT60_CIRCLE
R1, R12, R18, R24, R30, R36, R42, R48, R54, R63, R64, R65, R67: 1k; 0603
R2, R6, R13, R19, R25, R31, R37, R43, R49: 75k; 0603@1
R3, R7, R14, R20, R26, R32, R38, R44, R50: 61.9k; 0603@1
R4, R8, R15, R21, R27, R33, R39, R45, R51: 33K,1%; 0603@1
R5, R9, R16, R22, R28, R34, R40, R46, R52, R68, R69, R70, R71: 10k; 0603
R10, R11, R17, R23, R29, R35, R41, R47, R53: 0.05; 2512
R55, R56, R57, R58, R59, R60, R61, R62: 100; 0603
R66: 47k; 0603
R72: 5.25k; RES_0805
R73: 0; 0603
U$1, U$4, U$7, U$10, U$13, U$16, U$19, U$22, U$25: LMP2231; LMP2231_SOT23_5
U$2, U$5, U$8, U$11, U$14, U$17, U$20, U$23, U$26: LM385; LM385_SOT23
U$3, U$6, U$9, U$12, U$15, U$18, U$21, U$24, U$27: PMV30UN_MOS; PMV30UN_SOT23
U$30, U$31, U$32, U$33: M5
U$35, U$36, U$37: DSM7T; 7-SEGMENT_SMD
U$38: PIC16F676
U$39: 4.7UH_INDUCTOR
U$40, U$41, U$42: SOT_223; BC856BMB
VR1: 10k; TRIMPOT-SMD-TC33X

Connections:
1: R17.P$1 (1), U$9.DRAIN
5V_PWR: C21.1, R72.2, U$38.1, U$39.P$2, U$40.P$2 (E), U$41.P$2 (E), U$42.P$2 (E)
ALT_GND: 3.3V_BUCK.5 (GND), 3.3V_BUCK.9 (GND), C21.2, C23.2, C24.2, D11.A, R67.1, R69.1, R70.1, R71.1, R73.1, U$38.14
A_CNTL: R55.1, U$38.10
BUCK_ENABLE: 3.3V_BUCK.2 (EN), R68.1, R69.2
B_CNTL: R56.1, U$38.7
C_CNTL: R57.1, U$38.5
D_CNTL: R58.1, U$38.6
E_CNTL: R59.1, U$38.8
F_CNTL: R60.1, U$38.9
GND: C3.-, C19.2, CHARGE.2 (GND), D1.C, D10.A, MTR.2 (GND), R7.1, R73.2, U$4.IN-, U$5.-, U$5.FB, U$6.SOURCE, VR1.2 (WIPER), VR1.3 (CCW)
G_CNTL: R61.1, U$38.2
unnamed: D1.A, R1.1
unnamed: U$37.3 (G1-3), U$37.8 (G2-8), U$41.P$1 (C)
unnamed: C2.2, R12.2, U$1.OUT, U$3.GATE
unnamed: C1.-, C3.+, D2.C, R3.1, R6.2, R8.1, R10.P$2 (2), U$1.IN-, U$2.-, U$2.FB, U$3.SOURCE, U$4.IN+
unnamed: R2.1, R3.2, U$1.V+
unnamed: C2.1, R5.2, U$1.V-
unnamed: R4.2, R5.1, U$2.+
unnamed: U$36.3 (G1-3), U$36.8 (G2-8), U$42.P$1 (C)
unnamed: C4.2, R1.2, U$4.OUT, U$6.GATE
unnamed: R63.1, U$40.P$3 (B)
unnamed: R6.1, R7.2, U$4.V+
unnamed: C4.1, R9.2, U$4.V-
unnamed: R8.2, R9.1, U$5.+
unnamed: R10.P$1 (1), U$6.DRAIN
unnamed: R11.P$1 (1), U$3.DRAIN
unnamed: D2.A, R12.1
unnamed: R64.2, U$41.P$3 (B)
unnamed: C6.2, R18.2, U$7.OUT, U$9.GATE
unnamed: C1.+, C5.-, D3.C, R2.2, R4.1, R11.P$2 (2), R14.1, U$1.IN+, U$7.IN-, U$8.-, U$8.FB, U$9.SOURCE
unnamed: R13.1, R14.2, U$7.V+
unnamed: C6.1, R16.2, U$7.V-
unnamed: R15.2, R16.1, U$8.+
unnamed: R62.1, U$37.5 (DP-5)
unnamed: D3.A, R18.1
unnamed: R62.2, R64.1, U$38.13
unnamed: C8.2, R24.2, U$10.OUT, U$12.GATE
unnamed: C5.+, C7.-, D4.C, R13.2, R15.1, R17.P$2 (2), R20.1, U$7.IN+, U$10.IN-, U$11.-, U$11.FB, U$12.SOURCE
unnamed: R19.1, R20.2, U$10.V+
unnamed: C8.1, R22.2, U$10.V-
unnamed: R21.2, R22.1, U$11.+
unnamed: R23.P$1 (1), U$12.DRAIN
unnamed: D4.A, R24.1
unnamed: R63.2, U$38.12
unnamed: C10.2, R30.2, U$13.OUT, U$15.GATE
unnamed: C7.+, C9.-, D5.C, R19.2, R21.1, R23.P$2 (2), R26.1, U$10.IN+, U$13.IN-, U$14.-, U$14.FB, U$15.SOURCE
unnamed: R25.1, R26.2, U$13.V+
unnamed: C10.1, R28.2, U$13.V-
unnamed: R27.2, R28.1, U$14.+
unnamed: R29.P$1 (1), U$15.DRAIN
unnamed: D5.A, R30.1
unnamed: C19.1, D10.C, R66.2, U$38.3, VR1.1 (CW)
unnamed: C12.2, R36.2, U$16.OUT, U$18.GATE
unnamed: C9.+, C11.-, D6.C, R25.2, R27.1, R29.P$2 (2), R32.1, U$13.IN+, U$16.IN-, U$17.-, U$17.FB, U$18.SOURCE
unnamed: R31.1, R32.2, U$16.V+
unnamed: C12.1, R34.2, U$16.V-
unnamed: R33.2, R34.1, U$17.+
unnamed: R35.P$1 (1), U$18.DRAIN
unnamed: D6.A, R36.1
unnamed: R65.2, U$38.11
unnamed: C14.2, R42.2, U$19.OUT, U$21.GATE
unnamed: C11.+, C13.-, D7.C, R31.2, R33.1, R35.P$2 (2), R38.1, U$16.IN+, U$19.IN-, U$20.-, U$20.FB, U$21.SOURCE
unnamed: R37.1, R38.2, U$19.V+
unnamed: C14.1, R40.2, U$19.V-
unnamed: R39.2, R40.1, U$20.+
unnamed: R41.P$1 (1), U$21.DRAIN
unnamed: D7.A, R42.1
unnamed: U$35.3 (G1-3), U$35.8 (G2-8), U$40.P$1 (C)
unnamed: C16.2, R48.2, U$22.OUT, U$24.GATE
unnamed: C13.+, C15.-, D8.C, R37.2, R39.1, R41.P$2 (2), R44.1, U$19.IN+, U$22.IN-, U$23.-, U$23.FB, U$24.SOURCE
unnamed: R43.1, R44.2, U$22.V+
unnamed: C16.1, R46.2, U$22.V-
unnamed: R45.2, R46.1, U$23.+
unnamed: R47.P$1 (1), U$24.DRAIN
unnamed: D8.A, R48.1
unnamed: R65.1, U$42.P$3 (B)
unnamed: C18.2, R54.2, U$25.OUT, U$27.GATE
unnamed: C15.+, C17.-, D9.C, R43.2, R45.1, R47.P$2 (2), R50.1, U$22.IN+, U$25.IN-, U$26.-, U$26.FB, U$27.SOURCE
unnamed: R49.1, R50.2, U$25.V+
unnamed: C18.1, R52.2, U$25.V-
unnamed: R51.2, R52.1, U$26.+
unnamed: R53.P$1 (1), U$27.DRAIN
unnamed: D9.A, R54.1
unnamed: R55.2, U$35.7 (A-7), U$36.7 (A-7), U$37.7 (A-7)
unnamed: R56.2, U$35.6 (B-6), U$36.6 (B-6), U$37.6 (B-6)
unnamed: R57.2, U$35.4 (C-4), U$36.4 (C-4), U$37.4 (C-4)
unnamed: R58.2, U$35.2 (D-2), U$36.2 (D-2), U$37.2 (D-2)
unnamed: R59.2, U$35.1 (E-1), U$36.1 (E-1), U$37.1 (E-1)
unnamed: R60.2, U$35.9 (F-9), U$36.9 (F-9), U$37.9 (F-9)
unnamed: R61.2, U$35.10 (G-10), U$36.10 (G-10), U$37.10 (G-10)
unnamed: 3.3V_BUCK.4 (FB), R67.2, R72.1
unnamed: 3.3V_BUCK.8 (BST), C20.1
unnamed: 3.3V_BUCK.6 (FREQ), R70.2
unnamed: 3.3V_BUCK.3 (COMP), C22.1, C24.1
unnamed: C22.2, R71.2
SW: 3.3V_BUCK.1 (SW), C20.2, D11.C, U$39.P$1
VCC: 3.3V_BUCK.7 (VIN), C17.+, C23.1, CHARGE.1 (VCC), MTR.1 (VCC), R49.2, R51.1, R53.P$2 (2), R66.1, R68.2, U$25.IN+

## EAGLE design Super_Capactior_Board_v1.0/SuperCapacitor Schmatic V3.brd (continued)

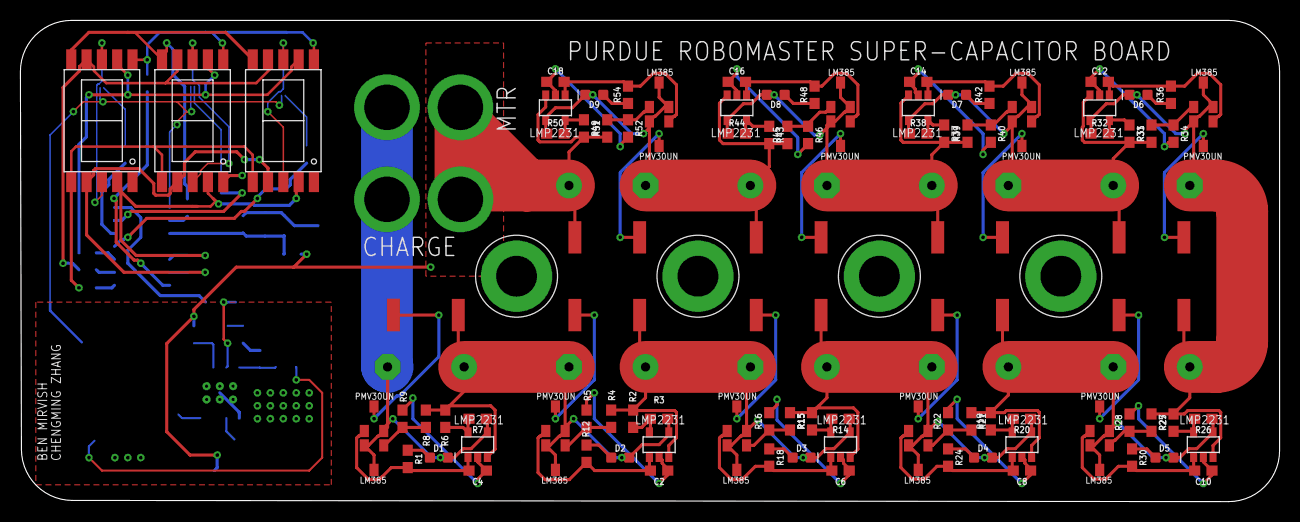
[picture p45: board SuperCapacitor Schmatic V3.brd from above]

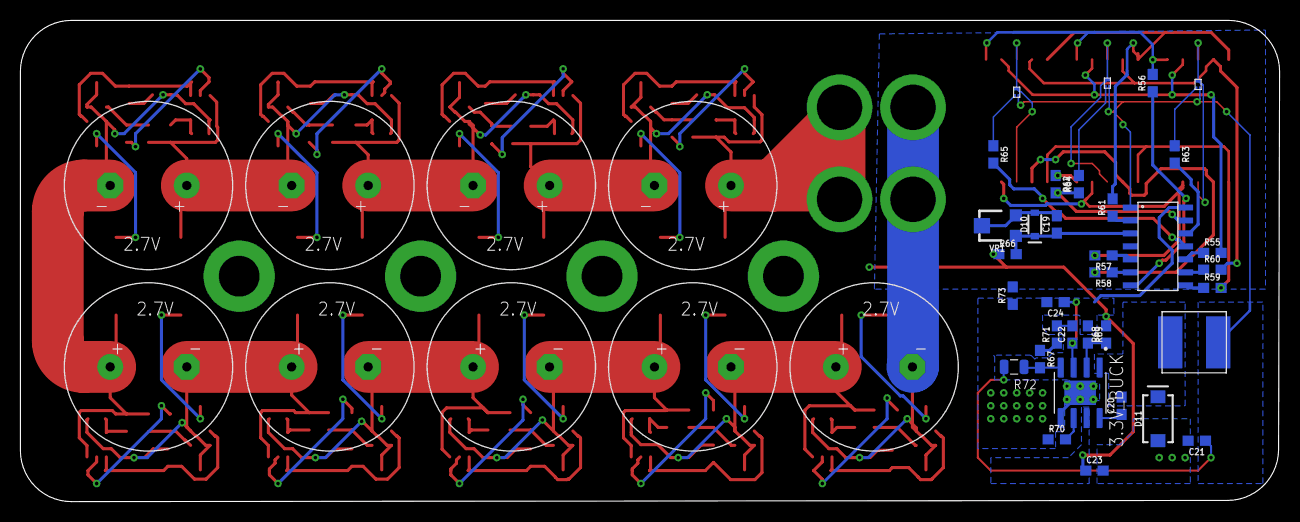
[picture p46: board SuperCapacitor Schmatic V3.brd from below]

Board: 2 copper layers, 123.4 x 47.2 mm, 151 parts (43 on the bottom side), 98 nets.

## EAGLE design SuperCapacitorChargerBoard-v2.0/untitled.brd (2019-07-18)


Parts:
BW_SEL_HIGHT_RES: SOLDERJUMPER; SOLDERJUMPER_ARROW_NOPASTE
C1, C3, C4, C5, C6, C7, C10, C11, C14, C15, C17, C18, C19, C23, C24, C26, C32, C41: 0.1uF; 0603
C2: 4.7uF; 0603
C8, C9, C21, C22, C25, C27, C28, C29, C30, C31, C40: 4.7uF; 1206
C12, C13: 22p; 0603-CAP
C16, C20, C33: 1nF; 0603
C34, C35, C36, C37, C38, C39: 22uF; 1206
CAP_CHARGING_CURRENT: ACS723; SO08
D1, D5: 3A/40V/500mV; SMA-DIODE
D2: RED; LED-0603
D3: GREEN; LED-0603
D4: MMSZ5242/12v; SOD-323
D6, D7: 1N4148WS; SOD323
FB1: 600Ω/1.8A; 0603
H_MOS: BSC018N04; TRANS_BSC076N06NS3-G
L1, L2: SWPA3012S4R7MT; L3230M
L3: WHC1265-10UH
LM5050: LM5050; TSOT-23-6-SOT-23-6
L_MOS: BSC018N04; TRANS_BSC076N06NS3-G
MOSFEL1: BSC018N04; TRANS_BSC076N06NS3-G
MOTOR_MOS: IRF4905S; D2PAK
MP2451, MP2451(2): MP2451; TSOT-23-6-SOT-23-6
MTR_OUT_CURRENT1: ACS723; SO08
PROGRAMMER: BM04B-GHS-TBT
Q1: S8050/25v 500mW; SOT23-3
Q2, Q3: NPN; SOT23-3
R1, R2: 10K; 0603
R3, R17: 100K; 0603
R4, R18: 124K; 0603
R5: 40.2k; 0603
R6, R8, R10: 16.2k; 0603
R7, R9, R11: 1.69k; 0603
R12, R13: 1k; 0603
R14, R16: 100; 0603
R15: 10k; 0603
R19: 8.87k; 0603
R20, R21: 470; 0603
R22, R23: 220; 0603
R24, R25, R26, R27: 10K; C0402
RESET: !RST; SWITCH-TACT-B3U-1100P-B
TOTAL_BAT_CURRENT: ACS723; SO08
TO_BAT: XT60PW-M; AMASS_XT60PW-M
TO_CAP: XT60PW-M; AMASS_XT60PW-M
TO_MOTOR: XT60PW-M; AMASS_XT60PW-M
U1: DUAL-OPTOISOLATOR_SOIC8; SO08
U$1: STM32F334K8T; QFP80P900X900X160-32N
U$6: MP1907GQ-Z; QFN10
USART: S4B-PH-SM4_TB
Y1: 16MHz; CRYSTAL-SMD-5X3.2-4PAD

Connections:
3V3_FB: MP2451.PIN3 (FB), R4.1, R5.2
12V_FB: MP2451(2).PIN3 (FB), R18.1, R19.2
BAT_VSENSE: C10.1, R6.1, R7.2, U$1.10 (PA4)
BW_SEL: BW_SEL_HIGHT_RES.2, CAP_CHARGING_CURRENT.6 (BW_SEL), MTR_OUT_CURRENT1.6 (BW_SEL), TOTAL_BAT_CURRENT.6 (BW_SEL)
CAP_CURRENT_SENSE: C16.1, CAP_CHARGING_CURRENT.7 (VIOUT), U$1.7 (PA1)
CAP_VSENSE: C11.1, R8.1, R9.2, U$1.11 (PA5)
DRV_EN: U$1.20 (PA10), U$6.6 (EN)
DRV_H: D6.A, H_MOS.4 (G), R20.2
DRV_HS_IN: U$1.18 (PA8), U$6.7 (INH)
DRV_L: D7.A, L_MOS.4 (G), R21.2
DRV_LS_IN: U$1.19 (PA9), U$6.8 (INL)
GND: BW_SEL_HIGHT_RES.1, C1.2, C2.2, C3.2, C4.2, C5.1, C7.1, C8.2, C9.2, C10.2, C11.2, C12.2, C13.2, C14.2, C15.2, C16.2, C17.2, C19.2, C20.2, C24.1, C25.2, C26.1, C28.2, C29.2, C30.2, C31.2, C32.2, C33.2, C34.2, C35.2, C36.2, C37.2, C38.2, C39.2, C40.2, C41.1, CAP_CHARGING_CURRENT.5 (GND), D1.A, D2.C, D3.C, D5.A, LM5050.PIN2 (GND), LM5050.PIN3 (OFF), L_MOS.1 (S), L_MOS.2 (S), L_MOS.3 (S), MP2451.PIN2 (GND), MP2451(2).PIN2 (GND), MTR_OUT_CURRENT1.5 (GND), PROGRAMMER.1, Q1.2 (E), Q2.2 (E), R2.1, R5.1, R7.1, R9.1, R11.1, R19.1, RESET.2, TOTAL_BAT_CURRENT.5 (GND), TO_BAT.2, TO_CAP.2, TO_MOTOR.2, U1.2 (C1), U1.5 (EM2), U$1.16 (VSS_2), U$1.32 (VSS_1)
IN_CURRENT_SENSE: C20.1, TOTAL_BAT_CURRENT.7 (VIOUT), U$1.6 (PA0)
LEDG: R13.1, U$1.27 (PB4)
LEDR: R12.1, U$1.26 (PB3)
MTR_CURRENT_SENSE: C33.1, MTR_OUT_CURRENT1.7 (VIOUT), U$1.8 (PA2)
MTR_EN: Q1.1 (B), U$1.14 (PB0)
unnamed: D2.A, R12.2
unnamed: MP2451.PIN4 (EN), R3.1
unnamed: D3.A, R13.2
unnamed: C6.1, MP2451.PIN1 (BST)
unnamed: C2.1, FB1.1, U$1.5 (VDDA/VREF)
unnamed: C6.2, D1.C, L1.1, MP2451.PIN6 (SW)
unnamed: R2.2, U$1.31 (BOOT0)
unnamed: Q1.3 (C), R14.2
unnamed: D4.A, MOTOR_MOS.1 (G), R14.1, R15.2
unnamed: C17.1, LM5050.PIN1 (VS), R16.1
unnamed: C18.2, C21.2, C22.2, U$6.9 (VSS)
unnamed: LM5050.PIN5 (GATE), MOSFEL1.4 (G)
unnamed: MP2451(2).PIN4 (EN), R17.1
unnamed: C23.1, MP2451(2).PIN1 (BST)
unnamed: C23.2, D5.C, L2.1, MP2451(2).PIN6 (SW)
unnamed: C27.1, U$6.3 (BST)
unnamed: D6.C, R20.1, U$6.4 (DRVH)
unnamed: R23.1, U1.1 (A1)
unnamed: D7.C, R21.1, U$6.10 (DRVL)
unnamed: R22.1, U1.3 (A2)
NRST: C1.1, R1.2, RESET.1, U$1.4 (NRST)
OSC_IN: C12.1, U$1.2 (PF0/OSC_IN), Y1.3 (2)
OSC_OUT: C13.1, U$1.3 (PF1/OSC_OUT), Y1.1
OUT1N: Q3.1 (B), R24.1, U1.8 (CL1)
OUT2N: Q2.1 (B), R25.1, U1.6 (CL2)
OUT_VSENSE: C14.1, R10.1, R11.2, U$1.12 (PA6)
PA3: U$1.9 (PA3)
PA7: U$1.13 (PA7)
PA11: U$1.21 (PA11)
PA12: U$1.22 (PA12)
PA15: U$1.25 (PA15)
PB1: U$1.15 (PB1)
PB5: U$1.28 (PB5)
RX: Q2.3 (C), R26.1, U$1.30 (PB7)
SIG_GND: Q3.2 (E), U1.4 (C2), U1.7 (EM1), USART.4 (JST4)
SIG_RX: R22.2, USART.3 (JST3)
SIG_TX: Q3.3 (C), R27.1, USART.2 (JST2)
SIG_VCC: R24.2, R27.2, USART.1 (JST1)
SYS_SWCLK: PROGRAMMER.2, U$1.24 (PA14)
SYS_SWDIO: PROGRAMMER.3, U$1.23 (PA13)
TX: R23.2, U$1.29 (PB6)
VBAT: C7.2, C24.2, LM5050.PIN6 (OUT), MOSFEL1.5 (D), MOSFEL1.6 (D), MOSFEL1.7 (D), MOSFEL1.8 (D), MOSFEL1.9 (D), MP2451.PIN5 (VIN), MP2451(2).PIN5 (VIN), R3.2, R6.2, R16.2, R17.2, TOTAL_BAT_CURRENT.1 (IP+), TOTAL_BAT_CURRENT.2 (IP+)
VBAT_RAW: LM5050.PIN4 (IN), MOSFEL1.1 (S), MOSFEL1.2 (S), MOSFEL1.3 (S), TO_BAT.1
VCAP: CAP_CHARGING_CURRENT.3 (IP-), CAP_CHARGING_CURRENT.4 (IP-), R8.2, TO_CAP.1
VCC: C3.1, C4.1, C5.2, C8.1, C9.1, C15.1, C19.1, C32.1, C40.1, C41.2, CAP_CHARGING_CURRENT.8 (VCC), FB1.2, L1.2, MTR_OUT_CURRENT1.8 (VCC), PROGRAMMER.4, R1.1, R4.2, R25.2, R26.2, TOTAL_BAT_CURRENT.8 (VCC), U$1.1 (VDD_1), U$1.17 (VDD_2)
VCC_12V: C18.1, C21.1, C22.1, C25.1, C26.2, L2.2, R18.2, U$6.1 (VDD)
VMTR: MTR_OUT_CURRENT1.3 (IP-), MTR_OUT_CURRENT1.4 (IP-), TO_MOTOR.1
VMTR_T: MOTOR_MOS.2 (D), MTR_OUT_CURRENT1.1 (IP+), MTR_OUT_CURRENT1.2 (IP+)
VOUT: C34.1, C35.1, C36.1, C37.1, C38.1, C39.1, CAP_CHARGING_CURRENT.1 (IP+), CAP_CHARGING_CURRENT.2 (IP+), D4.C, L3.P$2 (2), MOTOR_MOS.3 (S), R10.2, R15.1
VSW_NODE: C27.2, H_MOS.1 (S), H_MOS.2 (S), H_MOS.3 (S), L3.P$1 (1), L_MOS.5 (D), L_MOS.6 (D), L_MOS.7 (D), L_MOS.8 (D), L_MOS.9 (D), U$6.5 (SW)
VSW_T: C28.1, C29.1, C30.1, C31.1, H_MOS.5 (D), H_MOS.6 (D), H_MOS.7 (D), H_MOS.8 (D), H_MOS.9 (D), TOTAL_BAT_CURRENT.3 (IP-), TOTAL_BAT_CURRENT.4 (IP-)

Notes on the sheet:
TODO: Current MIght exceed ACS, BM04B port order not correct, bandwidth select
VBAT
VOUT
Main PWM Constant Power MOSFET
MOSFET DRIVER
MOTOR ENABLE CONTROLLER
Noisy System


Board: 4 copper layers, 66.0 x 63.2 mm, 103 parts (1 on the bottom side), 61 nets.

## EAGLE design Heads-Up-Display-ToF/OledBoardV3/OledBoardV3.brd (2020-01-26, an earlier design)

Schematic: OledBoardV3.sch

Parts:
C1, C2, C3, C4, C5, C6: 0.1uF; 0603
C7, C8, C24: 100nF; C0603
C25, C26: 1uF; C0603
D1: GREEN; LED-0603
D2: 1A/23V/620mV; SOD-323
D12, D13: Yellow; LED-0603
IC2: FT232RL; SSOP28-LD
L1: 4.7µH/±30%/1.2A; INDUCTOR_4.7UH
P2: 0475890001; MOLEX_0475890001
R1: 47k; 0603
R2: 1k; 0603
R3: 5.6k; 0603
R4: 100k; 0603
R5, R6, R25, R26, R27, R28: 1K; R0603
R29, R30: 10K; R0603
SV1: MA03-2
U1: AP3012; SOT23-5
U2: UG-2856KLBAG01_4WSPI; FPC05024-42201
U9: ATMEGA328P_TQFP; TQFP32-08
U$1, U$2, U$3, U$4: MOUNTINGHOLE2.5; MOUNTINGHOLE_2.5_PLATED
U$5, U$8: SM03B-GHS-TB
U$6: SS1P3L-M3/84A
U$9: XT30PW-M; XT30
U$16: CSTNE16M0VH3C000R0
U$17: KSR223GLFG

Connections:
3.3V: C1.1, C2.1, D1.A, IC2.17 (3V3OUT), L1.P$1 (1), U1.4 (!SHDN!), U1.5 (VIN), U2.P$5 (VDD), U2.P$6 (BS1)
12V: C3.1, C4.1, C5.1, D2.C, R1.2, U2.P$23 (VCC)
AMMO1: U9.23 (PC0(ADC0)), U$5.P$3 (1)
AMMO2: U9.24 (PC1(ADC1)), U$5.P$4 (2)
D+: IC2.15 (USBDP), P2.3 (D+)
D-: IC2.16 (USBDM), P2.2 (D-)
GND: C1.2, C2.2, C3.2, C4.2, C5.2, C6.2, C8.2, C24.2, C25.2, C26.2, IC2.7 (GND), IC2.18 (GND), IC2.21 (GND), IC2.25 (AGND), IC2.26 (TEST), P2.5 (GND), R2.1, R3.1, R4.1, R28.1, SV1.6, U1.2 (GND), U2.P$1 (GND), U2.P$2 (VLSS), U2.P$3 (VSS), U2.P$7 (BS2), U2.P$8 (!CS), U2.P$10 (D!C!/SA0), U2.P$11 (GND), U2.P$12 (GND), U2.P$16 (GND), U2.P$17 (GND), U2.P$18 (GND), U2.P$19 (GND), U2.P$20 (GND), U2.P$24 (GND), U9.3 (GND), U9.5 (GND), U9.21 (AGND), U$5.P$5 (3), U$8.P$5 (3), U$9.P$2 (GND), U$16.2 (GND), U$17.P$1 (1)
MISO: SV1.1, U9.16 (PB4(MISO))
MOSI: SV1.4, U9.15 (PB3(MOSI/OC2))
unnamed: D1.C, R2.2
unnamed: R1.1, R3.2, U1.3 (FB)
unnamed: C6.1, U2.P$22 (VCOMH)
unnamed: D2.A, L1.P$2 (2), U1.1 (SW)
unnamed: R4.2, U2.P$21 (IREF)
unnamed: C7.1, IC2.2 (!DTR)
unnamed: IC2.23 (!TXLED), R6.2
unnamed: IC2.22 (!RXLED), R5.2
unnamed: D13.C, R6.1
unnamed: D12.C, R5.1
unnamed: U9.7 (PB6(XTAL1/TOSC1)), U$16.1 (IN)
unnamed: U9.8 (PB7(XTAL2/TOSC2)), U$16.3 (OUT)
unnamed: C24.1, U9.20 (AREF)
unnamed: R27.2, U9.31 (PD1(TXD))
unnamed: R26.2, U9.30 (PD0(RXD))
RESET: C7.2, R25.1, SV1.5, U9.29 (PC6(/RESET)), U$17.P$2 (2)
RX: IC2.1 (TXD), R26.1, U$8.P$3 (1)
SCK: R28.2, SV1.3, U9.17 (PB5(SCK))
SCL: R30.2, U2.P$13 (SCLK/SCL), U9.28 (PC5(ADC5/SCL))
SDA: R29.2, U2.P$14 (SDIN/SDA), U2.P$15 (NC/D2), U9.27 (PC4(ADC4/SDA))
TX: IC2.5 (RXD), R27.1, U$8.P$4 (2)
VCC: C25.1, C26.1, D12.A, D13.A, IC2.4 (VCCIO), IC2.20 (VCC), R25.2, R29.1, R30.1, SV1.2, U9.4 (VCC), U9.6 (VCC), U9.18 (AVCC), U$6.P$1 (C), U$9.P$1 (VCC)
VUSB: C8.1, P2.1 (VCC), U$6.P$2 (A)

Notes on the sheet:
Boost 3.3v -> 12v
OLED
Connectors
Atmega
USB To Serial
USB


Board: 2 copper layers, 56.6 x 33.3 mm, 44 parts (0 on the bottom side), 32 nets.

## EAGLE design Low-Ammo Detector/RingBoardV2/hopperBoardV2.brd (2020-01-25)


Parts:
C1: 4.7uF; C0603
C2: 22pF; C0603
C3: 10uF; C0603
R1: 330k; R0603
R2: 180k; R0603
U$1, U$2: 2PIN
U$3, U$4: OPL550
U$5: TPS62260
U$6: SM02B-GHS-TB
U$8: SM03B-GHS-TB
U$9: 2.2uH; 74479776222

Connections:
1.5V: C2.1, C3.1, R1.2, U$1.P$2 (1.5V), U$2.P$2 (1.5V), U$9.P$2 (2)
5V: C1.1, U$3.P$3 (VCC), U$4.P$3 (VCC), U$5.P$1 (VCC), U$5.P$3 (EN), U$6.P$3 (1)
AMMO1: U$3.P$2 (OUT), U$8.P$4 (2)
AMMO2: U$4.P$2 (OUT), U$8.P$3 (1)
GND: C1.2, C3.2, R2.1, U$1.P$1 (GND), U$2.P$1 (GND), U$3.P$1 (GND), U$4.P$1 (GND), U$5.P$2 (GND), U$6.P$4 (2), U$8.P$5 (3)
unnamed: U$5.P$5 (SW), U$9.P$1 (1)
unnamed: C2.2, R1.1, R2.2, U$5.P$4 (FB)

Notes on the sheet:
Buck Converter 5v -> 1.5v
Laser1
Laser2
Power In
Connectors
To OLED
IR Laser


Board: 2 copper layers, 144.0 x 146.5 mm, 13 parts (0 on the bottom side), 7 nets.

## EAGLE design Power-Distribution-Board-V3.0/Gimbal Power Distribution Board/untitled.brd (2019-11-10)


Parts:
6A_CONNECTED, 8A_CONNECTED: 3V 20mA; LED-1206
6A_GND_SLIPRING, 6A_SLIPRING: S2B-PH-SM4_TB
8A_GND_SLIPRING, 8A_SLIPRING: S4B-PH-SM4_TB
AMMOBOOST: S2B-PH-SM4_TB
AMMOBOOST_OUT: XT30
AMMOFEED_CAN: BM02B-GHS-TBT(LF)(SN); BM02B-GHS-TBT_1
AMMO_10A: XT30
AMMO_DETECT_3V3: XT30
ATMEL_3V3: XT30
AUX_10A: XT30
AUX_CAN: BM02B-GHS-TBT(LF)(SN); BM02B-GHS-TBT_1
C1, C29: 22u; C1206
C2, C74: 0.1u; C0603
C3, C75: 150p; C0603
C4, C76: 10u; C1206
D1, D9: SMD-DIODE-SCHOTTKY-40V-3A(DO-214AB); DO-214AB
FLYWHEEL1_10A, FLYWHEEL2_10A: XT30
FLYWHEEL2_CAN: BM02B-GHS-TBT(LF)(SN); BM02B-GHS-TBT_1
FLYWHEEL_CAN: BM02B-GHS-TBT(LF)(SN); BM02B-GHS-TBT_1
GIMBAL_10A: XT30
GIMBAL_CAN: BM02B-GHS-TBT(LF)(SN); BM02B-GHS-TBT_1
L1, L4: 4.7u; MHCI0603-4R7M-R8
R1, R2: 1.2K; R2010
R3, R7: 40.2K; 0603
R4, R5, R87, R88: 100k; R0603
R6, R91: 24k; R0603
R8: 125K; 0603
R89: 560k; 0603
REFEREE_UART_STM32: S3B-PH-SM4_TB
REFEREE_UART_TX2: S3B-PH-SM4_TB
REFF, REFF1: 100k; R0603
REF_CAN_POW_OUT: S4B-PH-SM4_TB
REF_CAN_POW_SLIP_RING: S4B-PH-SM4_TB
SIGNALS_SLIPRING: S6B-PH-SM4_TB
STM32_24V: XT30
STM32_CAN: BM02B-GHS-TBT(LF)(SN); BM02B-GHS-TBT_1
TO_STM32: S3B-PH-SM4_TB
TX2_12V: XT30
U$1, U$2, U$4, U$49: MOUNTINGHOLE2.5; MOUNTINGHOLE_2.5_PLATED
U$3, U$5: MP1584_V2

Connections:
3V3: AMMO_DETECT_3V3.P$2 (VCC), ATMEL_3V3.P$2 (VCC), C1.1, L1.P$2 (2), R8.2
3V3EN: R5.1, R6.2, U$5.EN
6A: 6A_SLIPRING.1 (JST2), 6A_SLIPRING.2 (JST3), C4.1, C76.1, R2.2, R5.2, R88.2, STM32_24V.P$2 (VCC), U$3.VIN, U$5.VIN
8A: 8A_SLIPRING.1 (JST1), 8A_SLIPRING.2 (JST2), 8A_SLIPRING.3 (JST3), 8A_SLIPRING.4 (JST4), AMMO_10A.P$2 (VCC), AUX_10A.P$2 (VCC), FLYWHEEL1_10A.P$2 (VCC), FLYWHEEL2_10A.P$2 (VCC), GIMBAL_10A.P$2 (VCC), R1.2
12V: C29.1, L4.P$2 (2), R89.2, TX2_12V.P$2 (VCC)
12VEN: R88.1, R91.2, U$3.EN
AMMOBOOST: AMMOBOOST.1 (JST2), AMMOBOOST_OUT.P$2 (VCC)
BST: C74.1, U$3.BST
BST1: C2.1, U$5.BST
CAN_N: AMMOFEED_CAN.1, AUX_CAN.1, FLYWHEEL2_CAN.1, FLYWHEEL_CAN.1, GIMBAL_CAN.1, SIGNALS_SLIPRING.1 (JST1), STM32_CAN.1
CAN_P: AMMOFEED_CAN.2, AUX_CAN.2, FLYWHEEL2_CAN.2, FLYWHEEL_CAN.2, GIMBAL_CAN.2, SIGNALS_SLIPRING.2 (JST2), STM32_CAN.2
COMP_3V3: C3.1, U$5.COMP
COMP_12: C75.1, U$3.COMP
DIGI: SIGNALS_SLIPRING.3 (JST3), TO_STM32.2 (JST2)
ESP32_TX: SIGNALS_SLIPRING.4 (JST4), TO_STM32.1 (JST1)
FB_3V3: R7.2, R8.1, U$5.FB
FB_12: R3.2, R89.1, U$3.FB
FREQ: REFF.1, U$3.FREQ
FREQ1: REFF1.1, U$5.FREQ
GND: 6A_CONNECTED.C, 6A_GND_SLIPRING.1 (JST2), 6A_GND_SLIPRING.2 (JST3), 8A_CONNECTED.C, 8A_GND_SLIPRING.1 (JST1), 8A_GND_SLIPRING.2 (JST2), 8A_GND_SLIPRING.3 (JST3), 8A_GND_SLIPRING.4 (JST4), AMMOBOOST.2 (JST3), AMMOBOOST_OUT.P$1 (GND), AMMO_10A.P$1 (GND), AMMO_DETECT_3V3.P$1 (GND), ATMEL_3V3.P$1 (GND), AUX_10A.P$1 (GND), C1.2, C4.2, C29.2, C76.2, D1.1 (+), D9.1 (+), FLYWHEEL1_10A.P$1 (GND), FLYWHEEL2_10A.P$1 (GND), GIMBAL_10A.P$1 (GND), R3.1, R4.1, R6.1, R7.1, R87.1, R91.1, REFEREE_UART_STM32.3 (JST3), REFEREE_UART_TX2.3 (JST3), REFF.2, REFF1.2, STM32_24V.P$1 (GND), TO_STM32.3 (JST3), TX2_12V.P$1 (GND), U$3.GND, U$3.GND_B, U$5.GND, U$5.GND_B
unnamed: 6A_CONNECTED.A, R2.1
unnamed: 8A_CONNECTED.A, R1.1
unnamed: C3.2, R4.2
unnamed: C75.2, R87.2
REF_RX: REFEREE_UART_STM32.1 (JST1), REFEREE_UART_TX2.2 (JST2), SIGNALS_SLIPRING.5 (JST5)
REF_TX: REFEREE_UART_STM32.2 (JST2), REFEREE_UART_TX2.1 (JST1), SIGNALS_SLIPRING.6 (JST6)
RF1: REF_CAN_POW_OUT.4 (JST4), REF_CAN_POW_SLIP_RING.1 (JST1)
RF2: REF_CAN_POW_OUT.3 (JST3), REF_CAN_POW_SLIP_RING.2 (JST2)
RF3: REF_CAN_POW_OUT.2 (JST2), REF_CAN_POW_SLIP_RING.3 (JST3)
RF4: REF_CAN_POW_OUT.1 (JST1), REF_CAN_POW_SLIP_RING.4 (JST4)
SW: C74.2, D9.2 (-), L4.P$1 (1), U$3.SW
SW1: C2.2, D1.2 (-), L1.P$1 (1), U$5.SW



Board: 2 copper layers, 86.3 x 49.2 mm, 61 parts (26 on the bottom side), 32 nets.

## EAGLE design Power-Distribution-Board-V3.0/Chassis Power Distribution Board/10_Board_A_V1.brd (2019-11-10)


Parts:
3V3_INDICATOR: LED0805_NOOUTLINE; CHIPLED_0805_NOOUTLINE
10A_IN_24V: XT60PW-M; AMASS_XT60PW-M
AUX, AUX2: XT30
BAT_CONNECTED: 3V 20mA; LED-1206
BAT_REG_IN: XT60PW-M; AMASS_XT60PW-M
BAT_REG_OUT: XT60PW-M; AMASS_XT60PW-M
C5, C6, C7: 0.1uF; 0603
C8: 4.7uF; 1206
CAN1, CAN2, CAN3, CAN4, CAN5, CAN6: BM02B-GHS-TBT(LF)(SN); BM02B-GHS-TBT_1
CAN_IN: BM02B-GHS-TBT(LF)(SN); BM02B-GHS-TBT_1
CAP_IN_24V: XT60PW-M; AMASS_XT60PW-M
CAP_MODE_BY_PASS: SWITCH-SPDT-SMD-RIGHT-ANGLE; SWITCH_SPST_SMD_A
CAP_OUT_24V: XT60PW-M; AMASS_XT60PW-M
D1: 1N4148; SOD-323
D2: CAP_INDICATOR; CHIPLED_0805_NOOUTLINE
D3: 3A/40V/500mV; SMA-DIODE
L1: SWPA3012S4R7MT; L3230M
MOTOR1, MOTOR2, MOTOR3, MOTOR4: XT30
MP2451: MP2451; TSOT-23-6-SOT-23-6
Q1: MMBT2222; SOT23-R
Q2, Q3: NPN; SOT23-3
R1, R2: 220; 0603-RES
R3, R4, R5: 10K; 0603-RES
R6: 100; 0603-RES
R7: 100K; 0603
R8: 124K; 0603
R9: 40.2k; 0603
R10: 0; 1206
R11, R17, R19: 1K; 0805
R13: 1.2K; R2010
R18: 10K; 0805
RELAY: RELAY_G5LE; RELAY_G5LE-1
U1: OPTOISOLATOR-2SOIC8; SO08-2
U$1, U$2, U$4, U$49: MOUNTINGHOLE2.5; MOUNTINGHOLE_2.5_PLATED
U$3: S3B-PH-SM4_TB

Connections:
3V3_FB: MP2451.PIN3 (FB), R8.1, R9.2
BAT_24V: 10A_IN_24V.2, BAT_REG_IN.2, C7.2, CAP_IN_24V.2, MP2451.PIN5 (VIN), R7.2, R13.2
BAT_REG_24V: BAT_REG_OUT.2, RELAY.3 (O)
CAN_N: CAN1.1, CAN2.1, CAN3.1, CAN4.1, CAN5.1, CAN6.1, CAN_IN.1
CAN_P: CAN1.2, CAN2.2, CAN3.2, CAN4.2, CAN5.2, CAN6.2, CAN_IN.2
CAP_24V: CAP_OUT_24V.2, RELAY.4 (S)
CAP_OR_REG: CAP_MODE_BY_PASS.1 (O), Q3.3 (C), R6.1
GND: 10A_IN_24V.1, AUX.P$1 (GND), AUX2.P$1 (GND), BAT_CONNECTED.C, BAT_REG_IN.1, BAT_REG_OUT.1, CAP_IN_24V.1, CAP_OUT_24V.1, MOTOR1.P$1 (GND), MOTOR2.P$1 (GND), MOTOR3.P$1 (GND), MOTOR4.P$1 (GND), R10.2
IN1: R1.1, U$3.1 (JST1)
IN2: R2.1, U$3.2 (JST2)
LOW_GND: U1.2 (C1), U1.4 (C2), U$3.3 (JST3)
MOTOR_24V: AUX.P$2 (VCC), AUX2.P$2 (VCC), MOTOR1.P$2 (VCC), MOTOR2.P$2 (VCC), MOTOR3.P$2 (VCC), MOTOR4.P$2 (VCC), RELAY.1
unnamed: CAP_MODE_BY_PASS.2, R17.1
unnamed: R1.2, U1.1 (A1)
unnamed: R2.2, U1.3 (A2)
unnamed: MP2451.PIN4 (EN), R7.1
unnamed: C6.1, MP2451.PIN1 (BST)
unnamed: C6.2, D3.C, L1.1, MP2451.PIN6 (SW)
unnamed: 3V3_INDICATOR.A, R11.1
unnamed: BAT_CONNECTED.A, R13.1
unnamed: D1.A, D2.C, Q1.3 (C), RELAY.5 (2)
unnamed: Q1.1 (B), R17.2, R18.2
unnamed: D2.A, R19.1
OUT1N: Q3.1 (B), R3.1, U1.8 (CL1)
OUT2: Q2.3 (C), R5.1
OUT2N: Q2.1 (B), R4.1, U1.6 (CL2)
SIG_GND: 3V3_INDICATOR.C, C5.1, C7.1, C8.2, D3.A, MP2451.PIN2 (GND), Q1.2 (E), Q2.2 (E), Q3.2 (E), R9.1, R10.1, R18.1, U1.5 (EM2), U1.7 (EM1)
VCC: C5.2, C8.1, CAP_MODE_BY_PASS.3 (S), D1.C, L1.2, R3.2, R4.2, R5.2, R6.2, R8.2, R11.2, R19.2, RELAY.2 (1)

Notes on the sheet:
Opto

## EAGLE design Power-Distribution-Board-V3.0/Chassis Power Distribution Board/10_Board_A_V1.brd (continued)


Board: 2 copper layers, 105.1 x 56.1 mm, 55 parts (0 on the bottom side), 28 nets.

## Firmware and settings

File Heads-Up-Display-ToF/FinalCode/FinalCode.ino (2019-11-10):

/*
Author: Henry Silva
Notes:
    - The ToF sensors on the I2C multiplexer will initialized
    starting on port 0 and continue to the number of ToF sensors - 1
    so pay attention to the ports that the sensors are connected to

    - Code assumes that the front two ToF sensors are 0 and 1, the back sensors are 2 and 3, the left
    ToF sensor is 4, and the right  sensor is 5

    - Code will currently light up the wall that is close relative to the front of the robot, not to the driver's view
    TODO: HUD update is now dependant on the tof cycle time, find a way to get sensor readings faster
*/
#include <Wire.h>
#include <VL53L0X.h>
#include "HyperDisplay_UG2856KLBAG01.h"

#define TCAADDR 0x70 // address of the I2C multiplexer
#define NUM_SENSORS 2 // number of ToF sensors
#define OLED_PORT 2 // the port that the OLED is connected to on the I2C multiplexer
#define WALL_CLOSE 300 // a number in mm that will mean a wall is close
#define HUD_CYCLE 20 // HUD refresh rate in milliseconds
#define TOF_CYCLE 4 // time between ToF readings in milliseconds
#define NUM_READINGS 3 // number of ToF readings to take the average of
#define CLOSE_DISTANCE 300 // distance of a wall that is "close" in millimeters
#define RETICLE 6 // spacing of the ammo indicator crosshair

VL53L0X tofSensors[NUM_SENSORS]; // VL53L0X ToF sensor array
UG2856KLBAG01_I2C hud; // sparkfun transparent oled HUD

volatile boolean checkToF = false; // will be true when that ToF sensors will be checked
volatile boolean updateHud = false; // will be true when the HUD is updated
unsigned long currentTime; // current time in milliseconds
unsigned long previousTime; // time that has passed since last HUD cycle
int tofReadings[NUM_SENSORS * 5]; // 5 most recent ToF readings
int tofReadingNum = 0; // current number of ToF readings taken since last HUD refresh
double tofAverage[NUM_SENSORS]; // array of all most recent 5 ToF sensors readings
int currentState[NUM_SENSORS]; // the current state of a wall being close
int lastState[NUM_SENSORS]; // the last state of the tof sensor

void setup()
{
    // start serial and wire
    Serial.begin(9600);
    Serial.println("Starting Up");
    Wire.begin();
    Wire.setClock(400000);

    // initialize HUD
    Serial.println("Initializing HUD");
    tcaPortSelect(OLED_PORT);
    hud.begin(); // this will initialize oled with defaults
    for (int i = 0; i < 7; i++)
        hudUpdate(i, 1);
    Serial.println("HUD ready");

    // initialize all sensors
    Serial.println("Initializing ToF sensors");
    for (int i = 0; i < NUM_SENSORS; i++)
    {
        Serial.print("Sensor ");
        Serial.print(i);
        tcaPortSelect(i);
        VL53L0X tofSensor; // sensors on the current multiplexer port
        tofSensors[i] = tofSensor;
        tofSensors[i].init();
        tofSensors[i].setTimeout(500);
        tofSensors[i].setMeasurementTimingBudget(20000); // configuration for long range
        Serial.print(" Ready\n");
    }
    Serial.println("ToF sensors ready\n");
    tcaPortSelect(OLED_PORT);
    for (int i = 0; i < 7; i++)
        hudUpdate(i, 0);
}

void loop()
{
    // set timer equal to the current time
    currentTime = millis();

    //check if ToF senors should be checked
    if (currentTime - previousTime >= TOF_CYCLE)
    {
        //Serial.print("Interrupt ");
        //Serial.println(tofReadingNum + 1);
        checkToF = true;
        previousTime = currentTime;
    }

    if (checkToF)
    {
        for (int i = 0; i < NUM_SENSORS; i++)
        {
            tofReadings[(NUM_SENSORS * tofReadingNum) + i] = readToF(i);
            //Serial.print("Tof read ");
            //Serial.print(i);
            //Serial.print(": ");
            //Serial.print(tofReadings[i * tofReadingNum]);
            //Serial.println();
        }
        //Serial.println();
        tofReadingNum += 1;
        checkToF = false;
    }

    if (tofReadingNum > NUM_READINGS - 1)
    {
        tcaPortSelect(OLED_PORT);
        for (int i = 0; i < NUM_SENSORS; i++)
        {
            int tofTotal = 0; // total of last 5 sensor readings
            for (int j = 0; j < NUM_READINGS; j++)
            {
                tofTotal += tofReadings[i + (NUM_SENSORS * j)];
            }
            tofAverage[i] = tofTotal / NUM_READINGS;
            Serial.print("ToF Average " );
            Serial.print(i);
            Serial.print(": ");
            Serial.println(tofAverage[i]);
        }
        Serial.println();

        // update oled here
        for (int i = 0; i < NUM_SENSORS; i++)
        {
            if (tofAverage[i] <= CLOSE_DISTANCE)
            {
                currentState[i] = 1;
            }
            else
            {
                currentState[i] = 0;
            }
            if (currentState[i] != lastState[i])
            {
                Serial.println("HUD Update");
                hudUpdate(i, currentState[i]);
            }
            lastState[i] = currentState[i];
        }
        tofReadingNum = 0;
    }
}

void tcaPortSelect(uint8_t port)
{
    if (port > 7)
        return;
    
    Wire.beginTransmission(TCAADDR);
    Wire.write(1 << port);
    Wire.endTransmission();
}

void hudUpdate(int sensor, int state)
{
    if (sensor == 0)
    {
        if (state)
            showPixels(25, 62, 2, 1, 3);
        else
            clearPixels(25, 62, 2, 1, 3);
    }
    else if (sensor == 1)
    {
        if (state)
            showPixels(63, 100, 2, 1, 3);
        else
            clearPixels(63, 100, 2, 1, 3);
    }
    else if (sensor == 2)
    {
        if (state)
            showPixels(25, 62, 60, 1, 2);
        else
            clearPixels(25, 62, 60, 1, 2);
    }
    else if (sensor == 3)
    {
        if (state)
            showPixels(63, 100, 60, 1, 2);
        else
            clearPixels(63, 100, 60, 1, 2);
    }
    else if (sensor == 4)
    {
        if (state)
            showPixels(16, 48, 2, 0, 2);
        else
            clearPixels(16, 48, 2, 0, 2);
    }
    else if (sensor == 5)
    {
        if (state)
            showPixels(16, 48, 125, 0, 2);
        else
            clearPixels(16, 48, 125, 0, 2);
    }
    else if (sensor == 6)
    {
        if (state)
        {
            hud.pixelSet(64 - RETICLE, 32);
            hud.pixelSet(64 + RETICLE, 32);
            hud.pixelSet(64, 32 - RETICLE);
            hud.pixelSet(64, 32 + RETICLE);
        }
        else
        {
            hud.pixelClear(64 - RETICLE, 32);
            hud.pixelClear(64 + RETICLE, 32);
            hud.pixelClear(64, 32 - RETICLE);
            hud.pixelClear(64, 32 + RETICLE);
        }
    }
}
// start and stop for pixels, pos for the x or y cor to draw the line, rotation 1 = horizontal, 0 = vertical
void showPixels(int start, int stop, int pos, int rotation, int spacing)
{
    for (int i = start; i <= stop; i += spacing)
    {
        if (rotation)
            hud.pixelSet(i, pos);
        else
            hud.pixelSet(pos, i);
    }
}

// start and stop for pixels, pos for the x or y cor to draw the line, rotation 1 = horizontal, 0 = vertical
void clearPixels(int start, int stop, int pos, int rotation, int spacing)
{
    for (int i = start; i <= stop; i += spacing)
    {
        if (rotation)
            hud.pixelClear(i, pos);
        else
            hud.pixelClear(pos, i);
    }
}
int readToF(uint8_t port)
{
    tcaPortSelect(port);
    return tofSensors[port].readRangeSingleMillimeters();
}

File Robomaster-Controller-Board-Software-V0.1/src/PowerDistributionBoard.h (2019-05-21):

#ifndef PDP_H
#define PDP_H
/**
 * TODO Update to the newest pdp design; integrate temperature and ADC IC
 **/

// Include
#include <stdint.h>
#include <Arduino.h>

// Constant goes here

// Declaration goes here
class PDP {
    public:
        float getBatteryVoltage();
        float getCapacitorVoltage();
        float getBatteryCurrent();
        bool canBoost();

        // Note you can only read analog inputs on ADC #1 once WiFi has started
        // Include A2 A3 A4 13 33 32 
        // https://learn.adafruit.com/adafruit-huzzah32-esp32-feather/pinouts
        PDP(uint8_t vBattPin, uint8_t vCapPin, uint8_t iBattPin);
    private:
        uint8_t vBattPin;
        uint8_t vCapPin;
        uint8_t iBattPin;
        float vBoostRef;
        float vCapMax;
        float vBatMax;
        static const uint16_t ANALOG_RANGE = 4095;
        static const uint16_t CURRENT_REF = 500;
        static constexpr float CURRENT_RATIO = 0.004;
        static constexpr float VOLTAGE_MAX = 30.0;
        static const uint8_t CAPACITOR_MIN = 12;  // Minimum voltage for capacitor boosting, 12 V
};

#endif

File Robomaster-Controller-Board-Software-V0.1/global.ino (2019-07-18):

// Debug setting
#define DEBUG 

#include <stdint.h>

// I2C
#include <Wire.h>

// WIFI libraries
#include <WiFi.h>
#include <WiFiAP.h>

// mDNS for local domain name resolution
#include <ESPmDNS.h>
// Async library
#include <AsyncTCP.h>
#include <ESPAsyncWebServer.h>
#include <AsyncWebSocket.h>

// FS
#include <FS.h>
#include "SD.h"
#include <SPIFFS.h>
#include <SPIFFSEditor.h>

//Include Libraries
#include <Adafruit_MCP9808.h>
#include "Adafruit_MCP23008.h"
#include <RTClib.h>
#include "src/SDlogger.h"
#include "src/OledMonitor.h"
#include "src/PowerDistributionBoard.h"
#include "src/DistanceSensorManager.h"
#include "src/Audio.h"

#include "SoundData.h";
#include "XT_Dac_Audio.h";

//Defining Pins
#define VBATPIN 13
#define VCAPIN  32
#define IBATTPIN  A2
#define VRATIO 30.0
#define VMIN 1
#define TX 10
#define RX 11
#define RX2 16
#define TX2 17
<<<<<<< HEAD
#define BUZZ_PIN 25
=======
#define BUZZ_PIN A1
>>>>>>> 2a0e721e7c98d8998be17b936e16ca8e8b9d0fbb

// SD card
#define CHIP_SELECT 33

// Oled
// HUD
#define HUD_OLED_WIDTH 128
#define HUD_OLEDHEIGHT 64
#define HUD_OLED_ADDR 0X3D


// Debug oled
#define DEBUG_OLED_WIDTH 128 // OLED display width, in pixels
#define DEBUG_OLED_HEIGHT 32 // OLED display height, in pixels
#define DEBUG_OLED_ADDR 0x3C
#define DEBUG_OLED_RESET -1 // Reset pin # (or -1 if sharing Arduino reset pin)

// Debugging
#define LED_BUILTIN 2

// Define data structure
struct Measurement
{
  uint32_t timestamp;
  float vbatt;
  float vcap;
  float ibatt;
  float tempC;
  uint16_t ableBoost;
  uint16_t dist[6];
  uint16_t isLeftClaw;
  uint16_t isRightClaw;
};

union DataPacket
{
  struct Measurement rawData;
  byte serialized[38];
};

struct Measurement DefaultValue = {
  0, 0, 0, 1, 3, true, {3, 1, 0, 0, 1, 3}, true, true
};

struct Measurement currentMeasurement;
union DataPacket packet;
bool isAccessMeasurement = false;

// Sensors initialization
Adafruit_MCP9808 tempsensor = Adafruit_MCP9808();

// Oled
Adafruit_SSD1306 display(DEBUG_OLED_WIDTH, DEBUG_OLED_HEIGHT, &Wire, DEBUG_OLED_RESET);
OledMonitor monitor(&display, DEBUG_OLED_ADDR);

// RTC sensor
RTC_PCF8523 rtc;

// Power distribution board
PDP pdp(VBATPIN, VCAPIN, IBATTPIN);

// Distance Sensors
SensorManager manager;

// Digital Control
// Include Pneumatic system and limit switch
Adafruit_MCP23008 digitalControl;

const uint8_t pneumatic0 = 0;
const uint8_t pneumatic1 = 1;
const uint8_t pneumatic2 = 2;
const uint8_t pneumatic3 = 3;
const uint8_t limitSW1 = 4;
const uint8_t limitSW2 = 5;

// SD logger
SDloggerFactory SDlogger = SDloggerFactory();

// Web server
AsyncWebServer server(80);
AsyncWebSocket ws("/ws");

// Replace with your network credentials
const char* SSID     = "BoilerBot_Standard_1";
const char* PASSWORD = "TESTIRES";
const char* DOMAIN_NAME = "boilerbot";

// Websocket connection tracker
uint32_t broadcast_id = -1;

void readFile(fs::FS &fs, const char * path);

void notFound(AsyncWebServerRequest * request) {
    request->send(404, "text/plain", "Not found");
}

// Register a timer event function for instance
void onWsEvent(AsyncWebSocket * server, AsyncWebSocketClient * client, AwsEventType type, void * arg, uint8_t *data, size_t len){
  // Serial.println(type);
  if(type == WS_EVT_CONNECT){
    //client connected
    Serial.printf("ws[%s][%u] connect: %u\n", server->url(), client->id());
  } else if(type == WS_EVT_DISCONNECT) {
    //client disconnected
    Serial.printf("ws[%s][%u] disconnect: %u\n", server->url(), client->id());
    if (broadcast_id == client->id()) {
      broadcast_id = -1;
    }
  } else if(type == WS_EVT_ERROR) {
    //error was received from the other end
    Serial.printf("ws[%s][%u] error(%u): %s\n", server->url(), client->id(), *((uint16_t*)arg), (char*)data);
  } else if(type == WS_EVT_PONG) {
    //pong message was received (in response to a ping request maybe)
    Serial.printf("ws[%s][%u] pong[%u]: %s\n", server->url(), client->id(), len, (len)?(char*)data:"");
  } else if(type == WS_EVT_DATA) {
    #ifdef DEBUG
      Serial.printf("Broadcast id: %d\n", broadcast_id);
      Serial.printf("Client id: %d\n", client->id());
    #endif
    if (broadcast_id != -1 && broadcast_id != client->id()) {
      return;
    } else {
      broadcast_id = client->id();
      server->binaryAll(packet.serialized, sizeof(packet.serialized));
      Serial.printf("ws[%s][%u] sent response\n", server->url(), client->id());
    }
  }
}

//Function Protoypes
void setup() {
  // setup_temp();
  // setup_reg();
  // currentMeasurement = DefaultValue
<<<<<<< HEAD
    pinMode(LED_BUILTIN, OUTPUT);

    ledcAttachPin(BUZZ_PIN,0);
    ledcSetup(0, 1000, 8);

    // Serial & Monitor initialization
    Serial.begin(115200);
    Serial.println();
    monitor.init(&Serial);

    // AP setup
    Serial.println("Configuring access point...");
    WiFi.softAP(SSID);

    Serial.print("IP Address: ");
    Serial.println(WiFi.softAPIP());
    Serial.print("Hostname: ");
    Serial.println(WiFi.softAPgetHostname());
    Serial.print("Domain name: ");
    Serial.printf("%s.local\n", DOMAIN_NAME);

    // mDNS setup
    if (!MDNS.begin(DOMAIN_NAME)) {
        Serial.println("Error setting up MDNS responder!");
    }
    MDNS.addService("http", "tcp", 80);

    // Logger setup
    Serial.println("SD logger test");
    SDlogger.init(CHIP_SELECT);
    SDlogger.info(&Serial);
    DateTime now = rtc.now();
    char logfile[40];
    sprintf(logfile, "/log-%d-%d-%d-%d-%d-%d.boiler", now.year(), now.month(), now.day(), now.hour(), now.minute(), now.second());
    SDlogger.setFp(logfile, FILE_WRITE);

    // Initialize measurement
    currentMeasurement = DefaultValue;

    // RTC setup
    if (! rtc.begin()) {
      Serial.println("Couldn't find RTC");
      while (1);
    }

    // Temperature sensor init
    // if (! tempsensor.begin(0x18)) {
    //   Serial.println("Couldn't find MCP9808! Check your connections and verify the address is correct.");
    //   while (1);
    // }
    // Mode Resolution SampleTime
    //  0    0.5°C       30 ms
    //  1    0.25°C      65 ms
    //  2    0.125°C     130 ms
    //  3    0.0625°C    250 ms
    // tempsensor.setResolution(1);

    // FS
    SPIFFS.begin();
    server.serveStatic("/", SPIFFS, "/").setDefaultFile("index.htm");
    // server.serveStatic("/log", SD, "/")
=======
  pinMode(LED_BUILTIN, OUTPUT);

  // Serial & Monitor initialization
  Serial.begin(9600);
  Serial.println();
  monitor.init(&Serial);

  // AP setup
  Serial.println("Configuring access point...");
  WiFi.softAP(SSID);

  Serial.print("IP Address: ");
  Serial.println(WiFi.softAPIP());
  Serial.print("Hostname: ");
  Serial.println(WiFi.softAPgetHostname());
  Serial.print("Domain name: ");
  Serial.printf("%s.local\n", DOMAIN_NAME);

  // mDNS setup
  if (!MDNS.begin(DOMAIN_NAME)) {
      Serial.println("Error setting up MDNS responder!");
  }
  MDNS.addService("http", "tcp", 80);
>>>>>>> 2a0e721e7c98d8998be17b936e16ca8e8b9d0fbb
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

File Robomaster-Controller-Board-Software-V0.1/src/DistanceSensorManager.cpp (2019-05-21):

#include "DistanceSensorManager.h"

#define ADDRESS_DEFAULT 0x29

SensorManager::SensorManager(uint8_t TCAADDR) {
    managerAddr = TCAADDR;
}

void SensorManager::setupSensors(uint8_t config) {
    Serial.println("Setuping up sensors");
    for(uint8_t i = 0; i < NUM_SENSORS; i++) {
        tcaselect(i, managerAddr);
        VL53L0X sensor;
        sensors[i] = sensor;
        uint8_t data;
        Serial.printf("Manager: %xd, No: %d, Addr: %xd\n", managerAddr, i, ADDRESS_DEFAULT);
        if (Wire.writeTransmission(ADDRESS_DEFAULT, &data, 0, 1) == I2C_ERROR_OK) {
            Serial.printf("No. %d online\n", i);
            sensor.init();
            sensorStatus |= 1;
            sensorStatus <<= 1;
            sensor.setTimeout(500);
            switch (config)
            {
                default:
                case HIGH_SPEED:
                    sensor.setMeasurementTimingBudget(20000);
                    break;
                case LONG_RANGE:
                    // lower the return signal rate limit (default is 0.25 MCPS)
                    sensor.setSignalRateLimit(0.1);
                    // increase laser pulse periods (defaults are 14 and 10 PCLKs)
                    sensor.setVcselPulsePeriod(VL53L0X::VcselPeriodPreRange, 18);
                    sensor.setVcselPulsePeriod(VL53L0X::VcselPeriodFinalRange, 14);
                    break;
                case HIGH_ACCURACY:
                    sensor.setMeasurementTimingBudget(200000);
                    break;
                
            }
        } else {
            sensorStatus |= 0;
            sensorStatus <<= 1;
        }
        
    }
}

void SensorManager::getDistance(uint16_t* dst) {
    for(uint8_t i = 0; i < NUM_SENSORS; i++) {
        uint8_t selector = 1 << (NUM_SENSORS - i);
        // Sensor not online
        if (!(selector & sensorStatus)) {
            *(dst + i) = 0;
            continue;
        }
        tcaselect(i, managerAddr);
        VL53L0X sensor = sensors[i];
        *(dst + i) = sensor.readRangeSingleMillimeters();
    }
    // Serial.printf("Function: %p, %d\n", dst, *dst);
    return;
}

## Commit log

2019-01-28 Create Voltage Regulator Code
2019-02-02 initial upload
    [rm_supercap.kicad_pcb, rm_supercap.sch]
2019-02-08 Temperature Sensor
    This is the temperature sensor with the measured results displayed on LCD.
2019-02-16 Combine Voltage Regulater2
2019-02-22 schematic_2/2019
    The voltage regulator needs to be changed.
    LCD and I2C need to be added
    [arduino.sch]
2019-02-23 Sample code from Adafruit
2019-03-02 Add files via upload
    the voltage regulator will be changed later.
    [arduino.sch]
2019-03-08 This is PCB design for buck converter circuit.
2019-03-23 Create Combined_UART.ino
    From Arduino board to HUD system. Displaying Vbat, Vcap, Temp..
2019-03-25 Unzip buck converter design
    [MP1584cir.brd, MP1584cir.sch]
2019-03-25 Remove buck circuit zip file from github
2019-04-10 Set websocket to broad every connected device
2019-04-14 Integrate PDP measurement
    [out.csv]
2019-04-14 Remove files
    [arduino.sch]
2019-04-27 Rearrange development structure
    [out.csv]
2019-05-20 Add time of flight sensor manager
2019-07-18 added some circuit and updated old ones
    [BOM.csv, BOM.xlsx, out.csv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]
2019-09-14 update from Kevin's Local Files
    [BOM.csv, BOM.xlsx, sch.brd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]
2019-09-14 rename a bunch of stuff
    [BOM.csv, BOM.xlsx, MP1584cir.brd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]
2019-11-10 updated all power distribution board
    [10_Board_A_V1.brd, 10_Board_A_V1.sch, MP1584cir.brd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]
2019-11-10 re-orginize our folder structure
    [OledBoardSchematicV1.brd, OledBoardSchematicV1.sch, diodeBoard.brd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]
2019-11-10 added changes since repo changes
    [diodeBoard.brd, hopperBoard.brd, hopperBoard.sch]
2019-11-10 readme updated
    [10_Board_A_V1.brd, 10_Board_A_V1.sch, BOM.csv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]
2019-11-11 updated the readme
    [untitled.brd, untitled.sch]
2019-11-14 added changes that were left behind
    [OledBoardSchematicV1.brd, OledBoardSchematicV1.sch]
2019-12-07 Ammo Board V2
    [OledBoardSchematicV1.brd, hopperBoard.brd, hopperBoardV2.brd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]
2020-01-06 added project
    [atmega328pTest.sch]
2020-01-08 test board update
    [atmega328pTest.brd, atmega328pTest.sch]
2020-01-25 OLED board update
    [OledBoardV3.brd, OledBoardV3.csv, OledBoardV3.sch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]
2020-01-26 added notes
    [OledBoardV3.brd]
2020-02-11 fixed mistake by ben, approved for manufacturing
    [BOM.csv, BOM.xlsx, SuperCapacitor Schmatic V3.brd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]
2020-03-01 Kevin fixed the v4 controller board! Please review it carefully
    [Adafruit Feather STM32F405 Express.brd, Adafruit Feather STM32F405 Express.sch, Pin chart.xls]
2020-03-05 fixed batt power and usb-c power conflict in the Draft Folder
2020-03-06 Thursday Meeting changes to the brd, waiting for final submit
    [Adafruit Feather STM32F405 Express.brd, Adafruit Feather STM32F405 Express.sch, RMCB4.brd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]
2020-03-07 almost done kevin
    [RMCB4.brd, RMCB4.sch]
2020-03-07 Add files via upload
    Current incomplete parts list for new board
    [CB4_BOM.xlsx]
2020-03-07 Updated Schematic
    [RMCB4.brd, RMCB4.sch]
2020-03-08 final -kevin
    [CB4_BOM.xlsx, Pin chart.xls, RMCB4.brd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]
2020-03-08 3d file uploaded
    [RMCB4.f3d]
2020-03-08 added multiplexer board
    [RMMB.brd, RMMB.sch]
2020-03-10 Update readme.md
    Siyu updates I2C Address

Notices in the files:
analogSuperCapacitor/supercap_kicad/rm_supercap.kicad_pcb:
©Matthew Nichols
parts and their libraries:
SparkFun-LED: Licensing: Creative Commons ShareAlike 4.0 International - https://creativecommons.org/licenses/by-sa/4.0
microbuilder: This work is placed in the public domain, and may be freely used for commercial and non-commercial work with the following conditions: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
